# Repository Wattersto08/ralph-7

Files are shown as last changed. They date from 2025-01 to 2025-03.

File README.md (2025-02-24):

# Ralph VII

image infoimage info

## The Project

Ralph 7 is the latest itteration of an ongoing mobile platform, this is intended to serve as a basis for learning, a platform to build on, see [iRIS](https://github.com/Wattersto08/iris) and my [gps](https://github.com/Wattersto08/Ros2-GPS-VK-162) package so far. 

This is running the following hardware:

- RPI 4 running ubuntu mate 20.04 
- rplidar a1m8 for the lidar module
- intel RealSense d435i stereo camera 
- GL.inet router 
- waveshare powered usb hub 
- 3S lipo for power 
- VK-162 for gps output
- foxglove for non-linux platform control
- [Josh Newans](https://github.com/joshnewans) fantastic and simple to implement diffdrive ros2 control nodes. 

This project has taken heavy influence from Josh's tutorials and guides.

## Todo

This list is divided into specific lists to cover each remit of the project. 

### ROS2 goals 
- [ ] get the maploader working. 
- [ ] add logic to load the correct map based on initial GPS coordinates. 
- [ ] implement AMCL for navigation and mapping.
- [ ] tune AMCL for best performance.
- [ ] create a bigger map of my flat, ralph was for more than just the bedroom! 
- [ ] generate a new URDF based on the fusion 360 CAD model. 
- [ ] create bash script for initialising and installing all required packages and utils. 
- [ ] implement docker for porting to new [hardware](https://www.nvidia.com/en-gb/autonomous-machines/embedded-systems/jetson-orin/nano-super-developer-kit/) *hint hint* 

### Hardware goals 
- [x] look into new wheels for the platform, I fear the current foam RC wheels are not up to the job and are not performing well on carpeted surfaces. [these](https://www.amazon.co.uk/gp/product/B07F9SSSND/ref=ox_sc_act_title_1?smid=A10EGWLGS2DC0K&psc=1) look like great candidates.
- [ ] tune the PID and validate the ros2 control surfaces.
- [ ] more scientifically measure the correct pulses per revolution of the DC encoder motors. 
- [x] implement a uROS mcu to make the following objects availible within ros2: 
- [x] VBUS - battery voltage 
- [ ] some sort of local temperature and humidity measurements. 
*Acquired sensor, further work needed to get it intigrated*
- [x] add ros2 control of the 36 neopixel's used for the headlights and status LED's. 
- [ ] design an all new PCB for consolidating the various modules being used. 
- [ ] design / source a new castor wheel, the current one is generating a lot of resistance, amplifying the issue with the wheels. 
- [ ] order and validate the latest PCB. 
- [x] Fix Castor mount hight, currently too low. 
- [ ] add current motor controller parts to one large plate. 
- [x] add active cooling to the chassis. 
- [ ] Create mechanical BOM. 
- [ ] Create URDF folder within package

### PCB Design

As part of this project I have designed the following PCB:

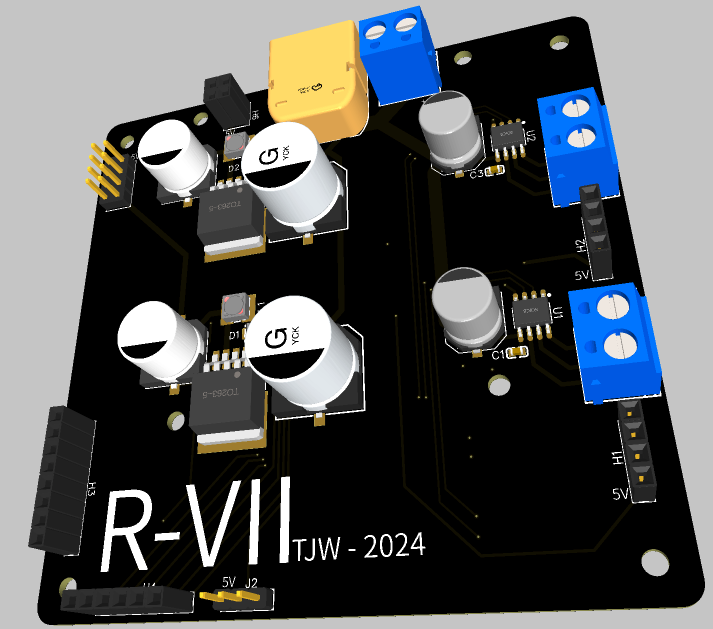
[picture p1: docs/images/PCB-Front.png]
image info
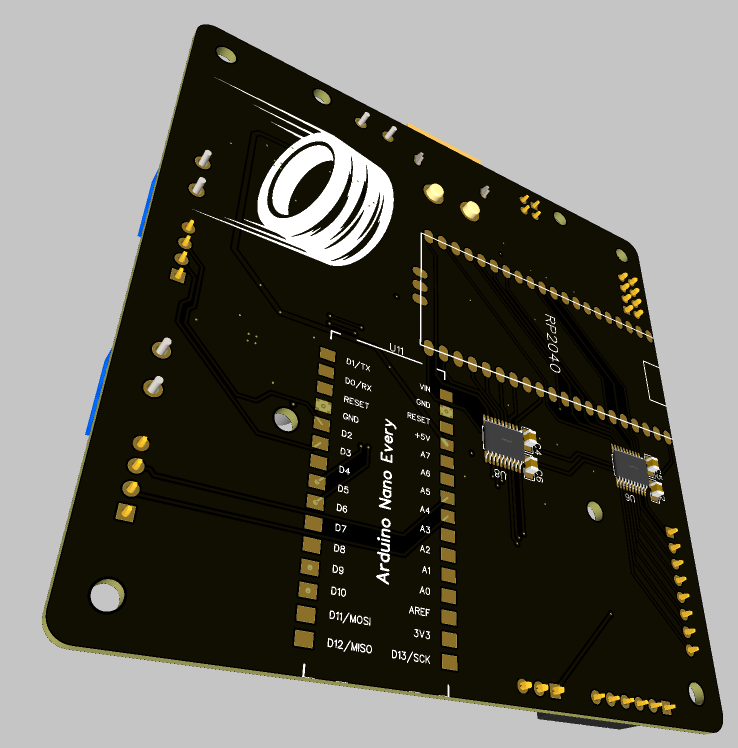
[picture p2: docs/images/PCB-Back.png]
image info


The gerber files and BOM can be found in /docs/PCB, this was designed in easyEDA and intended to be ordered from jlcpcb and lcsc electronics, this will make ordering and manufacturing straightforward. 

This aims to solve: 

- dedicated 5V4A psu for the RPI 
- dedicated 5V4A psu for auxillery devices
- upgraded DC motor control using [A4950ELJTR](https://www.lcsc.com/product-detail/Brushed-DC-Motor-Drivers_MSKSEMI-A4950ELJTR-T-MS_C7473144.html) brushed motor controllers, these are much more efficiant that the outdate L298n dual H-bridge being used at the moment. 
- adds a RPI pico 2 for uROS integration 
- solid mount points for the rpi 
- DC input for bench testing 
- XT60 jack for LIPO connection
- outputs for GPIO and neopixels. 

### Mechanical Design

all parts have been designed around [MakerBeam](https://www.makerbeam.com/) 10x10 Components, these are readily availible and server as a great base to build off. 

Prints were designed within Fusion 360 and printed in PLA on the bambulab P1S, STL's are in the Print Files dir.

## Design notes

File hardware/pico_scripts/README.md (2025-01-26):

## Pico Hardware Script

the files within this are taken from [joshnewans](https://github.com/joshnewans/microros_pico_ws) guide, and modified to control the following onboard the robot, current tasks being managed: 

- [x] VBUS monitoring 
- [x] NeoPixel headlight control 
- [ ] temperature and humidity control

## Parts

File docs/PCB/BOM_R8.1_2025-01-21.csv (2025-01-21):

ID | Name | Designator | Footprint | Quantity | Manufacturer Part | Manufacturer | Supplier | Supplier Part | Price | Pins
1 | 220nF | C1,C3 | C0603 | 2 | 0603B224K500NT | FH(风华) | LCSC | C83626 | 0.006 | 2
2 | 100uF | C7,C10 | CAP-SMD_BD12.5-L13.0-W13.0-RD | 2 | VKML1702C101MV | Ymin(永铭) | LCSC | C487477 | 0.498 | 2
3 | 1000uF | C8,C9 | CAP-SMD_BD10.0-L10.3-W10.3-FD | 2 | RVT1C102M1010 | HONOR(荣誉) | LCSC | C3359 | 0.107 | 2
4 | XT60PW-M | CN1 | CONN-TH_XT60PW-M | 1 | XT60PW-M | AMASS(艾迈斯) | LCSC | C98732 | 0.58 | 4
5 | SM340AF | D1,D2 | SMA-FL_L3.5-W2.5-LS4.6-L-RD | 2 | SM340AF | LRC(乐山无线电) | LCSC | C354996 | 0.039 | 2
6 | HDR-F-2.54_1x4 | H1,H2 | HDR-F-2.54_1X4 | 2 |  |  | LCSC | C225501 | 0.077 | 4
7 | HDR-F-2.54_1x8 | H3 | HDR-F-2.54_1X8 | 1 |  |  | LCSC | C225505 | 0.207 | 8
8 | HDR-F-2.54_1x6 | H4 | HDR-F-2.54_1X6 | 1 |  |  | LCSC | C40877 | 0.076 | 6
9 | HDR-F-2.54_2x2 | H6 | HDR-F-2.54_2X2 | 1 |  |  | LCSC | C239342 | 0.079 | 4
10 | HDR-M-2.54_2x4 | J1 | HDR-M-2.54_2X4 | 1 |  |  | LCSC | C58363 |  | 8
11 | HDR-M-2.54_1x3 | J2 | HDR-M-2.54_1X3 | 1 |  |  | LCSC | C180248 | 0.19 | 3
12 | 100uH | L1,L2 | IND-SMD_L4.2-W4.2_PIS3D18P | 2 | PIS3D18P-101M-T | EMTEK(兆欣) | LCSC | C251760 | 0.227 | 2
13 | WJ300V-5.0-2P | P1,P2,P3 | CONN-TH_2P-P5.00_WJ300V-5.00-2P | 3 | WJ300V-5.0-2P | KANGNEX(康奈克斯电气) | LCSC | C8385 | 0.082 | 2
14 | 250mΩ | R1,R2 | R2512 | 2 | 25121WF250LT4E | UNI-ROYAL(厚声) | LCSC | C25467 | 0.033 | 2
15 | A4950ELJTR-T-MS | U1,U2 | SOIC-8_L4.9-W3.9-P1.27-LS6.0-BL-EP | 2 | A4950ELJTR-T-MS | MSKSEMI(美森科) | LCSC | C7473144 | 0.441 | 9
16 | 100uF | U3,U4 | CAP-SMD_BD8.0-L8.3-W8.3-LS9.1-FD | 2 | RVT1H101M0810 100UF 50V | DMBJ(振宝佳) | LCSC | C970687 | 0.104 | 2
17 | LM2576S-5.0 | U9,U10 | TO-263-5_L10.2-W8.9-P1.70-BR | 2 | LM2576S-5.0 | UMW(友台半导体) | LCSC | C347413 | 0.575 | 6
18 | 100nF | C2,C4,C5,C6 | C0805 | 4 | CC0805KRX7R9BB104 | YAGEO(国巨) | LCSC | C49678 | 0.005 | 2
19 | TXB0108PWR | U8,U6 | TSSOP-20_L6.5-W4.4-P0.65-LS6.4-BL | 2 | TXB0108PWR | TI(德州仪器) | LCSC | C53406 | 0.269 | 20
20 | RPI Pico | U7 | RPI PICO | 1 | RP2040 |  | Digi-Key |  |  | 43
21 | ARDUINO_NANO_EVERY HEADER 1*15 2.54 COPY | U11 | ARDUINO NANO EVERY NO HOLE | 1 | ABX00028 | Arduino |  | 301-50-884 |  | 30

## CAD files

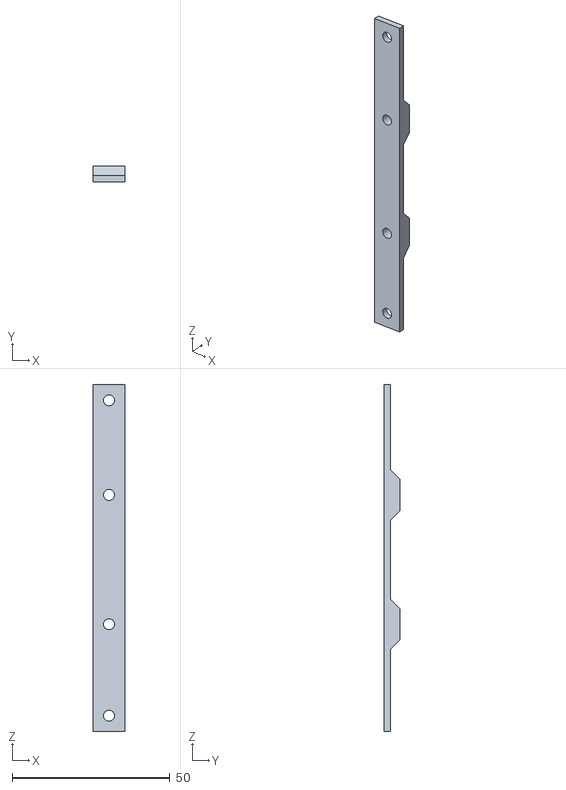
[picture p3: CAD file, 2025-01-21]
docs/Print Files/Nano Mount V2.stl
10.0 x 5.00 x 110.0

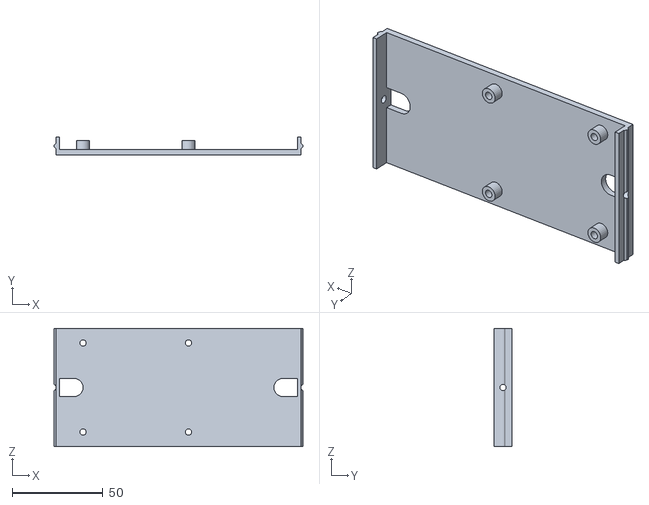
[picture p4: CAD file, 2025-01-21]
docs/Print Files/Pi Mount V3.stl
137.0 x 10.0 x 65.0

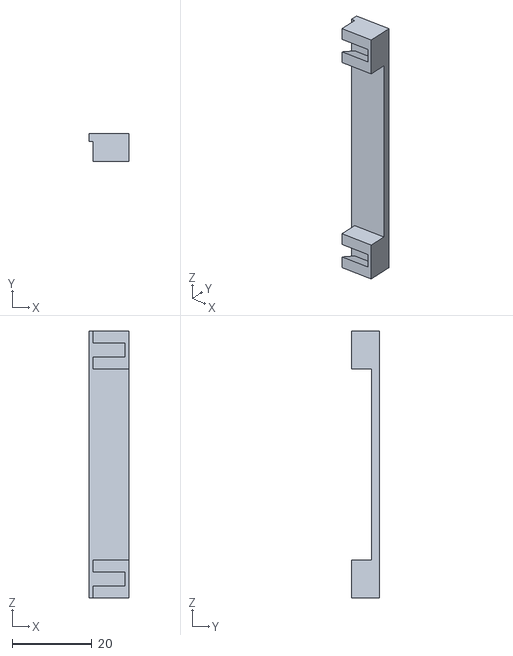
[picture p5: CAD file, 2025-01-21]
docs/Print Files/Batt Mount Clip.stl
10.0 x 7.00 x 67.0

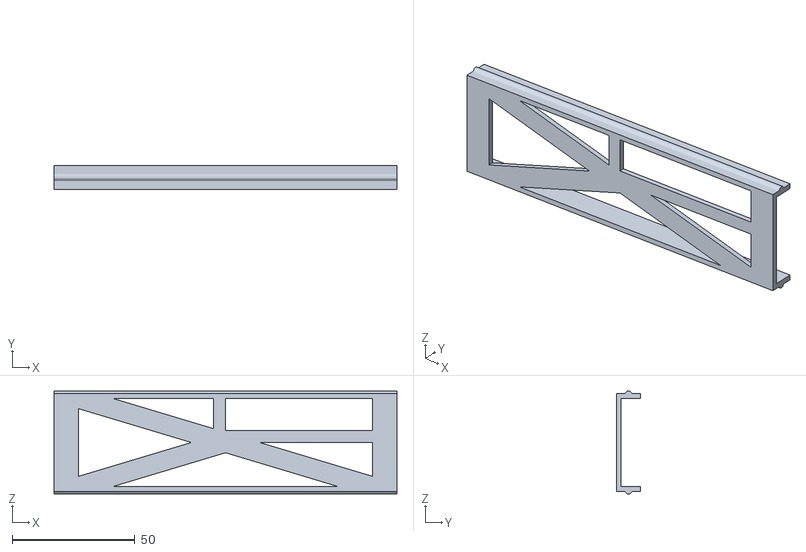
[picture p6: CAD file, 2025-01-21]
docs/Print Files/140mm Panel with cutout.stl
140.0 x 10.0 x 42.0

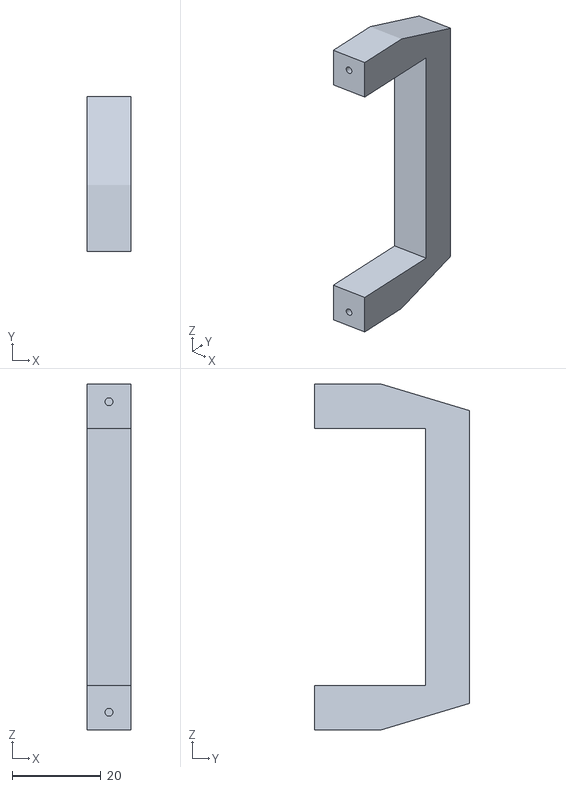
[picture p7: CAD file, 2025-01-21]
docs/Print Files/Router Clip.stl
10.0 x 35.0 x 78.0

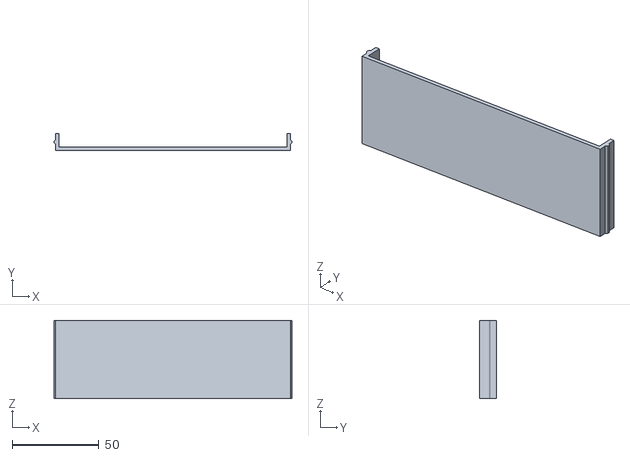
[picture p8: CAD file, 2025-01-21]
docs/Print Files/Base Blank Plate 45mm.stl
137.0 x 10.0 x 45.0

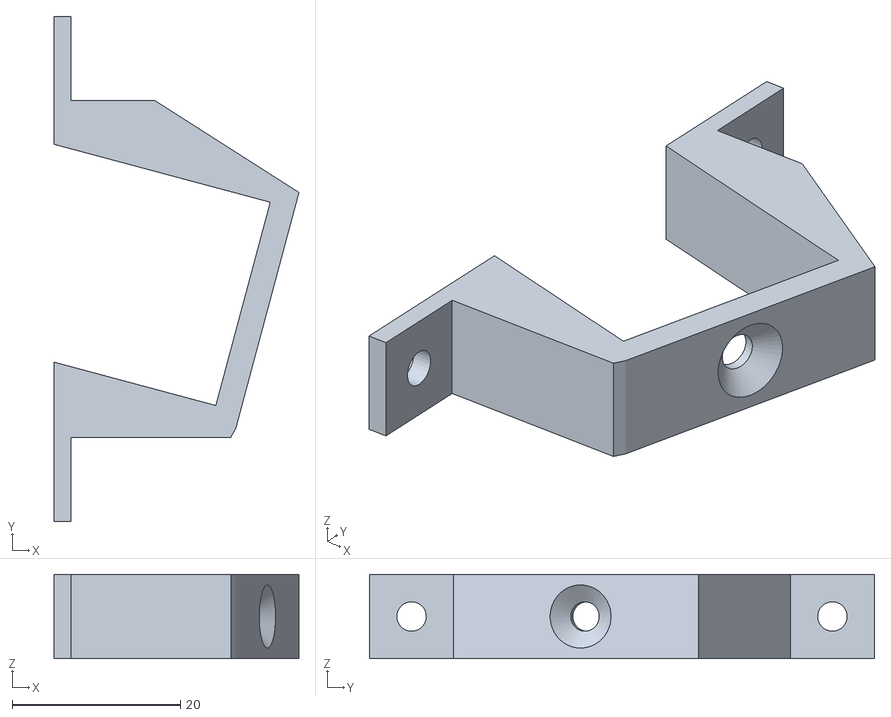
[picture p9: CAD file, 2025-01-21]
docs/Print Files/RealSense Mount.stl
29.1 x 60.0 x 10.0

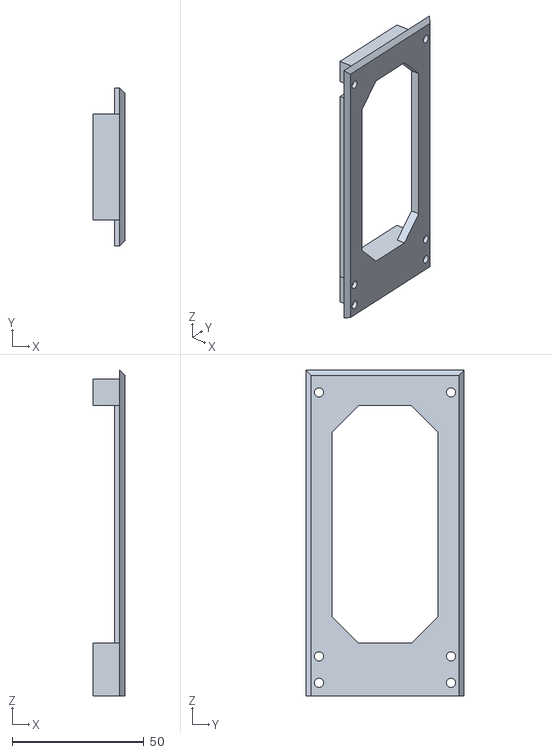
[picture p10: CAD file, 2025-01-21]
docs/Print Files/Wheel Outer V2.stl
12.0 x 60.0 x 123.5

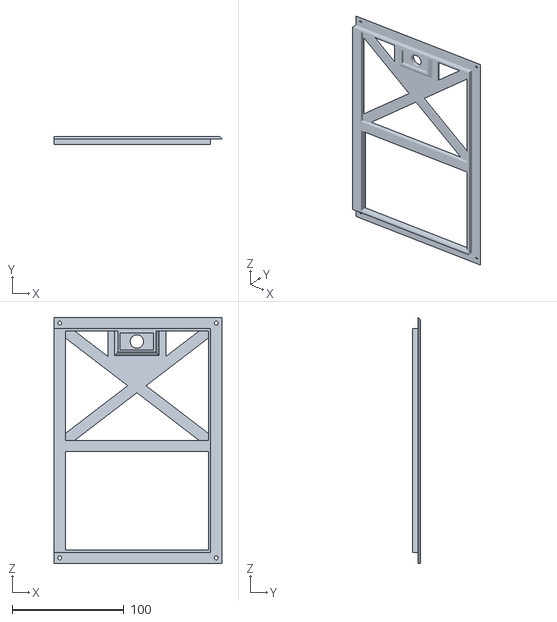
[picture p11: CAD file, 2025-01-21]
docs/Print Files/Top Plate R.stl
150.0 x 7.00 x 220.0

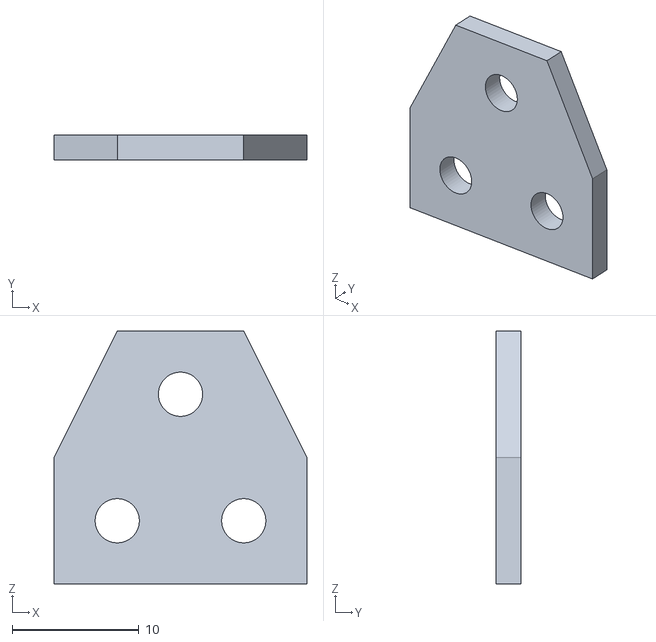
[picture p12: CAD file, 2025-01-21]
docs/Print Files/T Piece Flat.stl
20.0 x 2.00 x 20.0

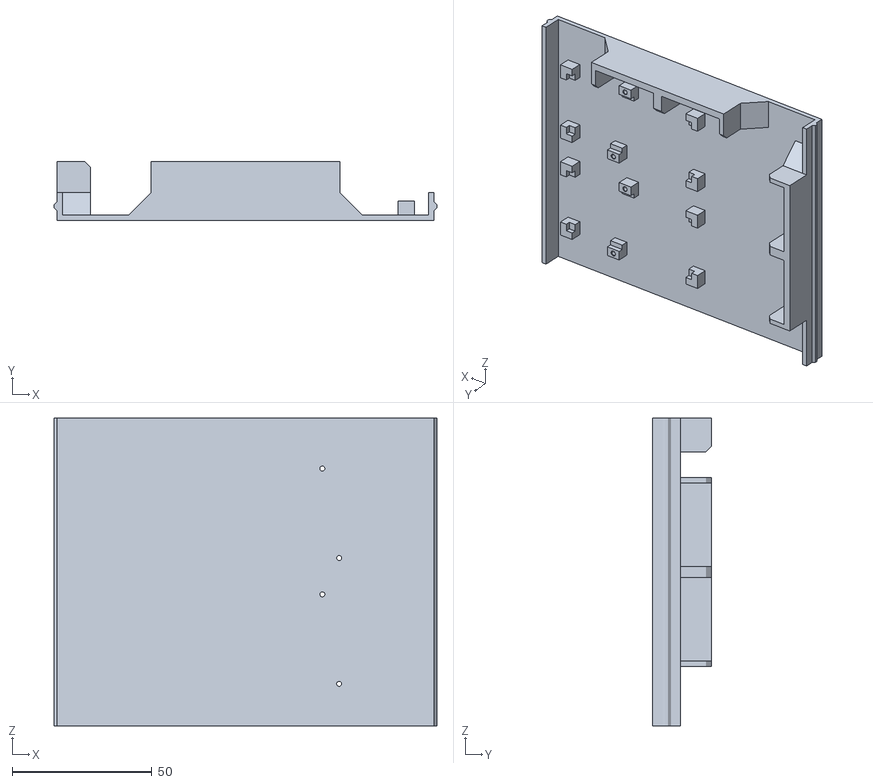
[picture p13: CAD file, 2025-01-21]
docs/Print Files/PS distribution plate.stl
137.0 x 21.0 x 110.0

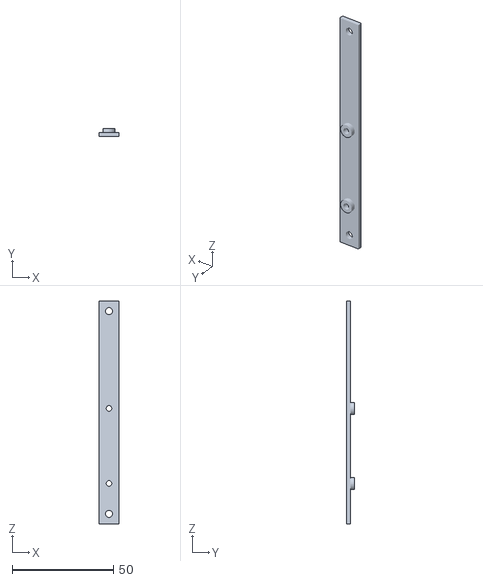
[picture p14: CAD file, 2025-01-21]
docs/Print Files/L298 Mount V2.stl
10.0 x 4.00 x 110.0

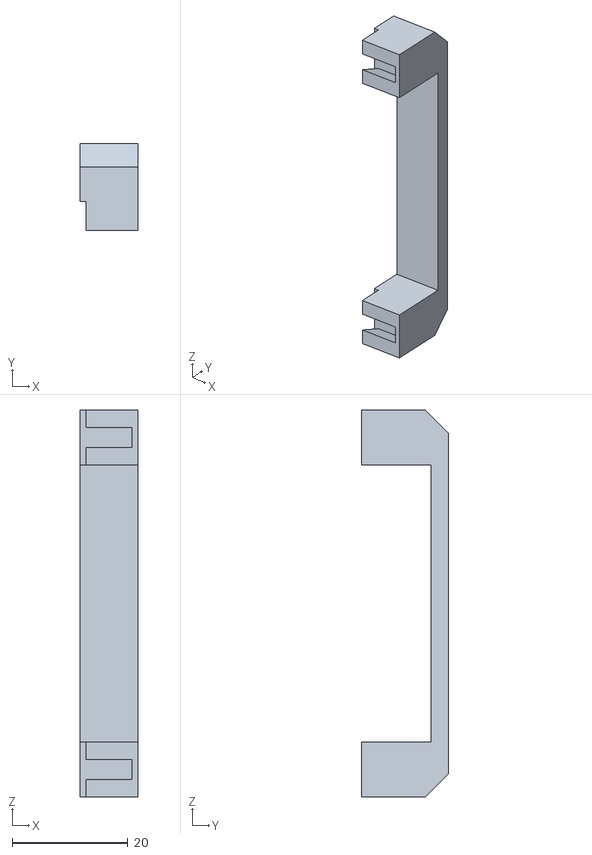
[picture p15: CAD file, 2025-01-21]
docs/Print Files/Battery Clip V2.stl
10.0 x 15.0 x 67.0

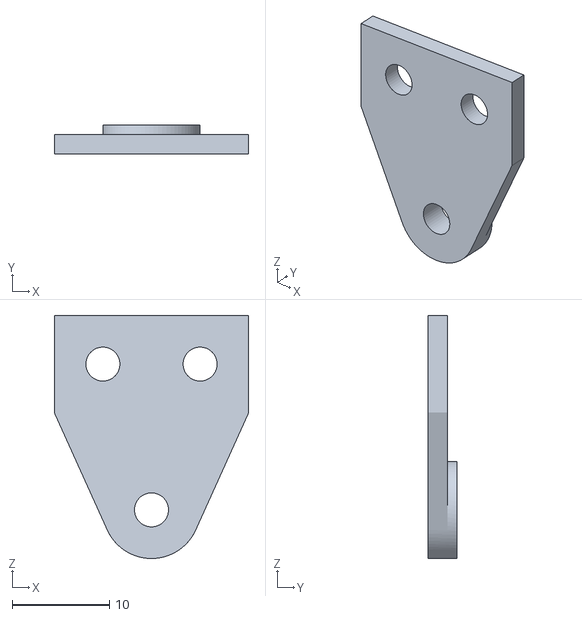
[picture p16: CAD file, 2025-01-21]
docs/Print Files/RP ACCESSORY.stl
20.0 x 3.00 x 25.0

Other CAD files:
docs/Print Files/Top Plate L.stl
docs/Print Files/GPS Holddown V2.stl
docs/Print Files/Fore - Top plate.stl
docs/Print Files/Castor V3.stl
docs/Print Files/180 Side Panel V2.stl
docs/Print Files/Base Blank Plate 25mm.stl
docs/Print Files/Battery Mount.stl
docs/Print Files/Corner Pieces V2.stl
docs/Print Files/GPS Mount V3.stl
docs/Print Files/HeadLight V5 L.stl
docs/Print Files/HeadLight V5 R.stl
docs/Print Files/M2 Side Clamps.stl
docs/Print Files/M2X2mm Spacer.stl
docs/Print Files/Pi Standoff.stl
docs/Print Files/RPLIDAR mount v2.stl
docs/Print Files/Router Mount V2.stl
docs/Print Files/USB HUB mount v2.stl
docs/Print Files/Wheel Calibration Tool.stl
docs/Print Files/XT60 Mount.stl

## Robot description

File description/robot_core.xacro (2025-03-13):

<?xml version="1.0"?>
<robot xmlns:xacro="http://www.ros.org/wiki/xacro">

  <material name="white">
    <color rgba="1 1 1 1"/>
  </material>

  <material name="green">
    <color rgba="0.06 0.256 0.1 1"/>
  </material>

  <material name="orange">
    <color rgba="1 0.3 0.1 1"/>
  </material>

  <material name="blue">
    <color rgba="0.2 0.2 1 1"/>
  </material>

  <material name="black">
    <color rgba="0 0 0 1"/>
  </material>

  <link name="base_link">
  </link>

  <link name="base_footprint">
  </link>
  <joint name="base_footprint_joint" type="fixed">
      <parent link="base_link"/>
      <child link="base_footprint"/>
      <origin xyz="0 0 0" rpy="0 0 0"/>
  </joint>

  <joint name="chassis_joint" type="fixed">
      <parent link="base_link"/>
      <child link="chassis"/>
      <origin xyz="-0.267 0 0"/>
  </joint>

  <link name="chassis">
      <visual>
          <origin xyz="0.152 0 0.031" rpy="0 0 0"/>
          <geometry>
              <box size="0.322 0.304 0.1"/>
          </geometry>
          <material name="green"/>
      </visual>
      <collision>
        <origin xyz="0.152 0 0.031" rpy="0 0 0"/>
        <geometry>
            <box size="0.322 0.304 0.1"/>
        </geometry>
      </collision>
  </link>

<!-- LEFT WHEEL -->

  <joint name="left_wheel_joint" type="continuous">
      <parent link="base_link"/>
      <child link="left_wheel"/>
      <origin xyz="0 0.125 0.005" rpy="-${pi/2} 0 0"/>
      <axis xyz="0 0 1"/>
  </joint>

  <link name="left_wheel">
      <visual>
          <geometry>
              <cylinder length="0.04" radius="0.042" />
          </geometry>
          <material name="black"/>
      </visual>
      <collision>
          <geometry>
              <cylinder length="0.04" radius="0.042" />
          </geometry>
      </collision>
  </link>

<!-- RIGHT WHEEL -->

  <joint name="right_wheel_joint" type="continuous">
      <parent link="base_link"/>
      <child link="right_wheel"/>
      <origin xyz="0 -0.125 0.005" rpy="${pi/2} 0 0"/>
      <axis xyz="0 0 -1"/>
  </joint>

  <link name="right_wheel">
      <visual>
          <geometry>
              <cylinder length="0.04" radius="0.042" />
          </geometry>
          <material name="black"/>
      </visual>
      <collision>
          <geometry>
              <cylinder length="0.04" radius="0.042" />
          </geometry>
      </collision>
  </link>

<!-- CASTER WHEEL -->

  <joint name="caster_wheel_joint" type="fixed">
      <parent link="chassis"/>
      <child link="caster_wheel"/>
      <origin xyz="-0.013 0 -0.00475" rpy="0 0 0"/>
  </joint>

  <link name="caster_wheel">
      <visual>
          <geometry>
              <sphere radius="0.0125" />
          </geometry>
          <material name="white"/>
      </visual>
      <collision>
          <geometry>
              <sphere radius="0.0125" />
          </geometry>
          <material name="white"/>
      </collision>
  </link>

</robot>

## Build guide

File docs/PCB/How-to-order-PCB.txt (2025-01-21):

How to Order PCB

Please refer to:
https://docs.easyeda.com/en/PCB/Order-PCB

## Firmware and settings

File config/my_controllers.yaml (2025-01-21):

controller_manager:
  ros__parameters:
    update_rate: 30

    diff_cont:
      type: diff_drive_controller/DiffDriveController

    joint_broad:
      type: joint_state_broadcaster/JointStateBroadcaster

diff_cont:
  ros__parameters:

    publish_rate: 50.0

    base_frame_id: base_link

    left_wheel_names: ['left_wheel_joint']
    right_wheel_names: ['right_wheel_joint']
    wheel_separation: 0.262
    wheel_radius: 0.0325

    use_stamped_vel: false

    # open_loop: false    

    # wheels_per_side: x
    # wheel_separation_multiplier: x
    # left_wheel_radius_multiplier: x
    # right_wheel_radius_multiplier: x

    # odom_frame_id: x
    # pose_covariance_diagonal: x
    # twist_covariance_diagonal: x
    # open_loop: x
    # enable_odom_tf: x

    # cmd_vel_timeout: x
    # publish_limited_velocity: x
    # velocity_rolling_window_size: x
    

    # linear.x.has_velocity_limits: false
    # linear.x.has_acceleration_limits: false
    # linear.x.has_jerk_limits: false
    # linear.x.max_velocity: NAN
    # linear.x.min_velocity: NAN
    # linear.x.max_acceleration: NAN
    # linear.x.min_acceleration: NAN
    # linear.x.max_jerk: NAN
    # linear.x.min_jerk: NAN

    # angular.z.has_velocity_limits: false
    # angular.z.has_acceleration_limits: false
    # angular.z.has_jerk_limits: false
    # angular.z.max_velocity: NAN
    # angular.z.min_velocity: NAN
    # angular.z.max_acceleration: NAN
    # angular.z.min_acceleration: NAN
    # angular.z.max_jerk: NAN
    # angular.z.min_jerk: NAN




# joint_broad:
#   ros__parameters:

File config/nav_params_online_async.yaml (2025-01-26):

slam_toolbox:
  ros__parameters:

    # Plugin params
    solver_plugin: solver_plugins::CeresSolver
    ceres_linear_solver: SPARSE_NORMAL_CHOLESKY
    ceres_preconditioner: SCHUR_JACOBI
    ceres_trust_strategy: LEVENBERG_MARQUARDT
    ceres_dogleg_type: TRADITIONAL_DOGLEG
    ceres_loss_function: None

    # ROS Parameters
    odom_frame: odom
    map_frame: map
    base_frame: base_footprint
    scan_topic: /scan
    use_map_saver: true
    mode: localization

    # if you'd like to immediately start continuing a map at a given pose
    # or at the dock, but they are mutually exclusive, if pose is given
    # will use pose
    map_file_name: /home/ralph/r7_ws/src/R7/maps/currentmap
    map_start_pose: [0.018495563826182507, -0.12486516718408672, 0.0]
    map_start_at_dock: true

    debug_logging: false
    throttle_scans: 1
    transform_publish_period: 0.02 #if 0 never publishes odometry
    map_update_interval: 5.0
    resolution: 0.05
    min_laser_range: 0.0 #for rastering images
    max_laser_range: 20.0 #for rastering images
    minimum_time_interval: 0.5
    transform_timeout: 0.2
    tf_buffer_duration: 30.
    stack_size_to_use: 40000000 #// program needs a larger stack size to serialize large maps
    enable_interactive_mode: true

    # General Parameters
    use_scan_matching: true
    use_scan_barycenter: true
    minimum_travel_distance: 0.5
    minimum_travel_heading: 0.5
    scan_buffer_size: 10
    scan_buffer_maximum_scan_distance: 10.0
    link_match_minimum_response_fine: 0.1  
    link_scan_maximum_distance: 1.5
    loop_search_maximum_distance: 3.0
    do_loop_closing: true 
    loop_match_minimum_chain_size: 10           
    loop_match_maximum_variance_coarse: 3.0  
    loop_match_minimum_response_coarse: 0.35    
    loop_match_minimum_response_fine: 0.45

    # Correlation Parameters - Correlation Parameters
    correlation_search_space_dimension: 0.5
    correlation_search_space_resolution: 0.01
    correlation_search_space_smear_deviation: 0.1 

    # Correlation Parameters - Loop Closure Parameters
    loop_search_space_dimension: 8.0
    loop_search_space_resolution: 0.05
    loop_search_space_smear_deviation: 0.03

    # Scan Matcher Parameters
    distance_variance_penalty: 0.5      
    angle_variance_penalty: 1.0    

    fine_search_angle_offset: 0.00349     
    coarse_search_angle_offset: 0.349   
    coarse_angle_resolution: 0.0349        
    minimum_angle_penalty: 0.9
    minimum_distance_penalty: 0.5
    use_response_expansion: true

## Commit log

2025-01-21 added mapping config, changes to the TF tree and updated the robot bringup launch
    [robot_core.xacro]
2025-01-21 added realsense launch for initial configuration
    [robot.urdf.xacro]
2025-01-21 added all mechanical files and updated README
    [140mm Panel with cutout.stl, 180 Side Panel V2.stl, BOM_R8.1_2025-01-21.csv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]
2025-01-26 added micro-ros agent, added basic nav2 mapping
    [robot.urdf.xacro, robot_core.xacro]
2025-02-24 updated robot description and added new hardware script for fan and headlight contol
    [lidar.xacro, robot_core.xacro]
2025-03-09 latest changes
    [lidar.xacro]
2025-03-13 Added depth camera functionality
    [depth_sensor.xacro, robot.urdf.xacro, robot_core.xacro]
